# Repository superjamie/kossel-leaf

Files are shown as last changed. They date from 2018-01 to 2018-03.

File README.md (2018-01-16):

# Kossel Leaf

Kossel Leaf is a carriage system for Kossel-style delta robot 3D printers.

It uses 3D printed components, OpenBuilds-style V-wheels, OpenBuilds-style 20mm V-slot aluminium extrusions, and standard metric fasteners.

The carriage is designed to drop in place of an existing Hiwin-style MGN12H (or MGN12C) rail system, only increasing the printer’s `DELTA_RADIUS` by 0.05mm.

Kossel Leaf uses a 3D printed leaf spring to keep two wheels under tension and pressed against the extrusion firmly and evenly at all points along vertical travel, like a [SeeMeCNC Cheapskate carriage](https://www.seemecnc.com/products/injection-molded-cheapskate-carriage-set).

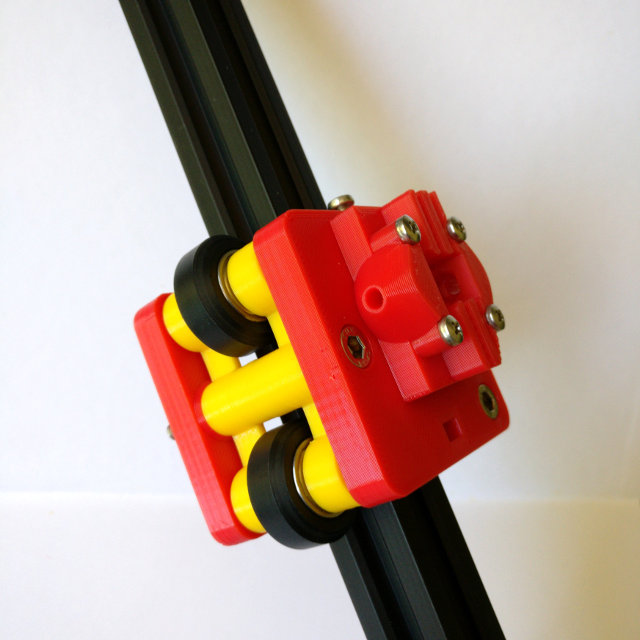
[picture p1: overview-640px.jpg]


See the included instruction manual for full BOM and assembly instructions.

## License

[CERN OHL v1.2](http://ohwr.org/cernohl)

## Author

Jamie Bainbridge - jamie.bainbridge@gmail.com

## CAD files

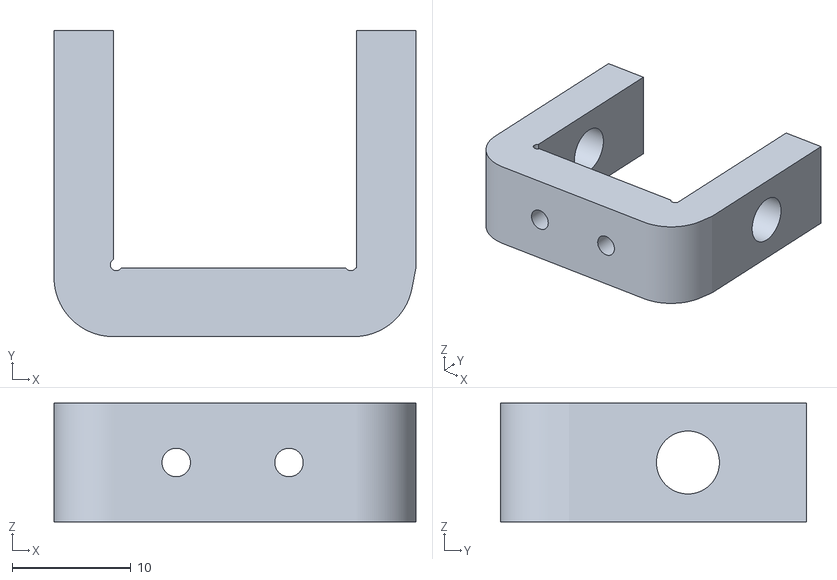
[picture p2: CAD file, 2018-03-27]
Endstop Holder for Omron SS-5GL.stl
30.5 x 25.8 x 10.0

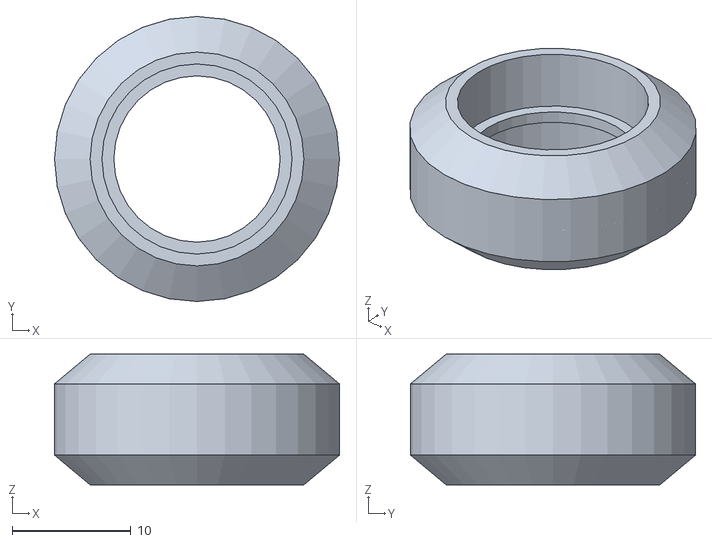
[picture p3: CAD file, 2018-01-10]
scad/parts/_wheel.stl
24.0 x 24.0 x 11.0

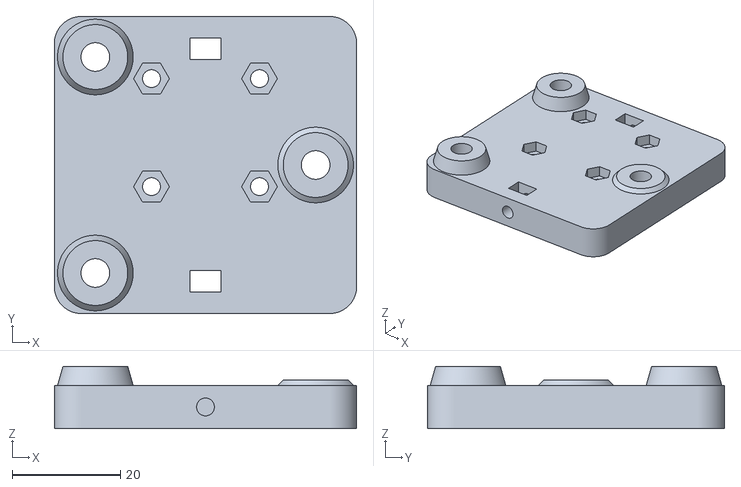
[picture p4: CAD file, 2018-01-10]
Carriage Inner.stl
56.0 x 55.0 x 11.5

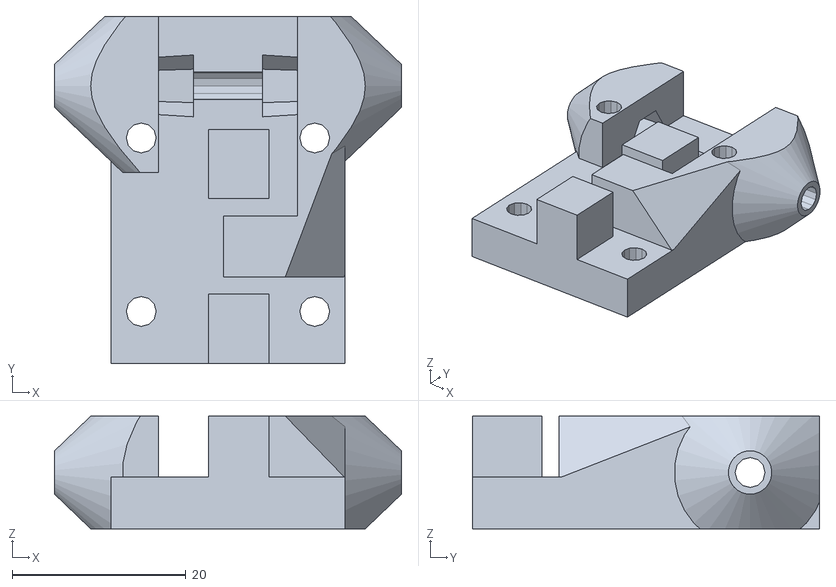
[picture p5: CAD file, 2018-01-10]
scad/parts/_belt-arm_johann.stl
40.0 x 40.0 x 13.0

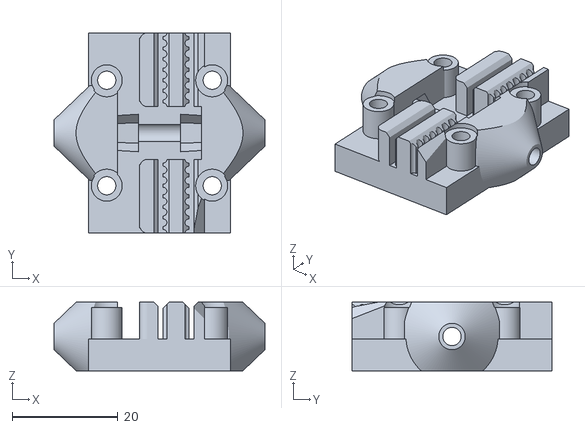
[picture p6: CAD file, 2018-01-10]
Kossel Leaf Mini 40mm Belt-Arm MGN12H.stl
40.0 x 38.0 x 13.0

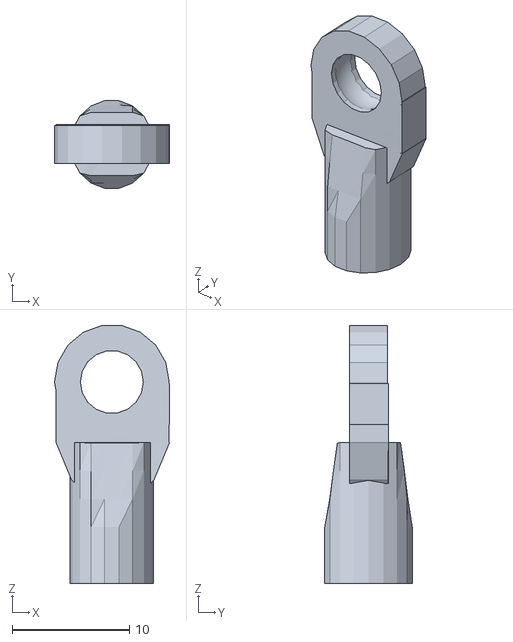
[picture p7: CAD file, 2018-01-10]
scad/parts/_tx5347.stl
9.81 x 7.47 x 22.0

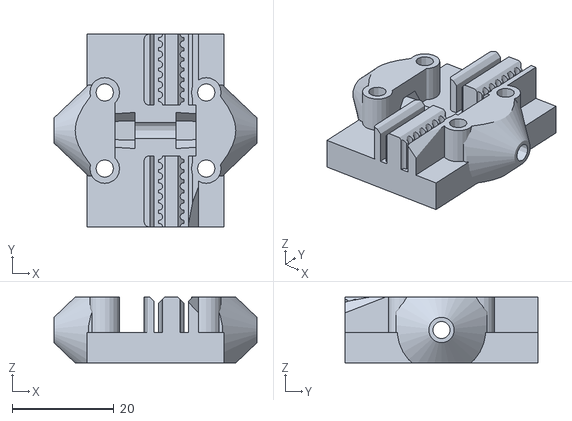
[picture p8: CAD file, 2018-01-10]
scad/parts/_belt-arm_schlotzz.stl
40.0 x 38.0 x 13.0

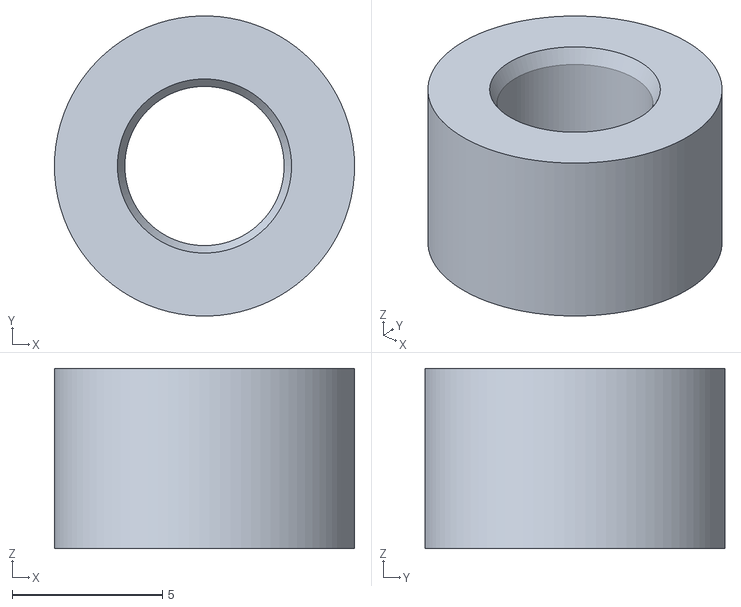
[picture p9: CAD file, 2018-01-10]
Spacer.stl
10.0 x 9.99 x 6.00

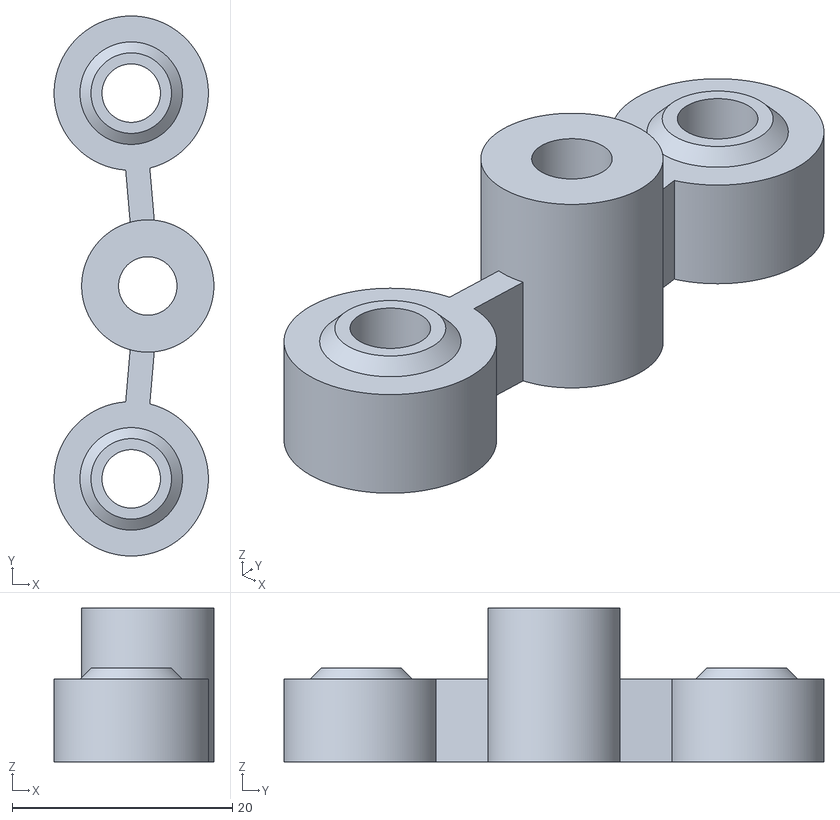
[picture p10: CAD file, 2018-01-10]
Leaf Spring Part 1 Alternate (2.2mm leaf, 1.5mm inset).stl
14.5 x 49.0 x 13.9

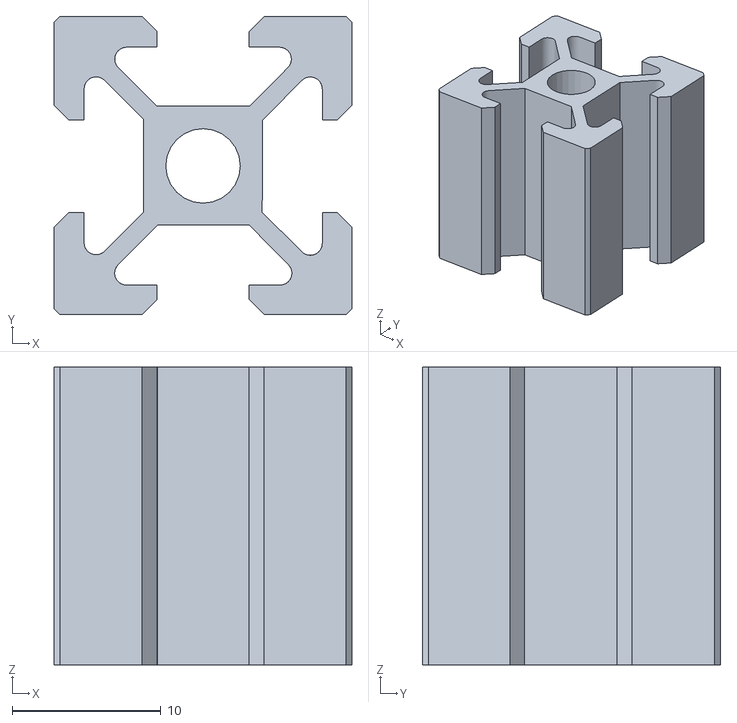
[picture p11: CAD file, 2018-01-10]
scad/parts/_vslot.stl
20.0 x 20.0 x 20.0

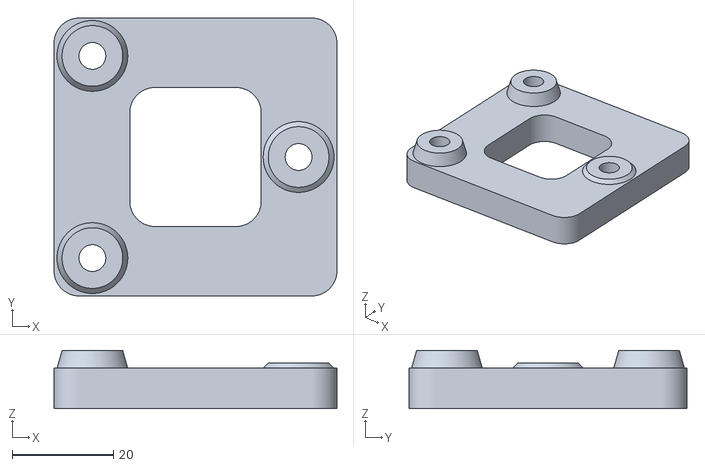
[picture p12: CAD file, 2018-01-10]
Carriage Outer.stl
56.0 x 55.0 x 11.5

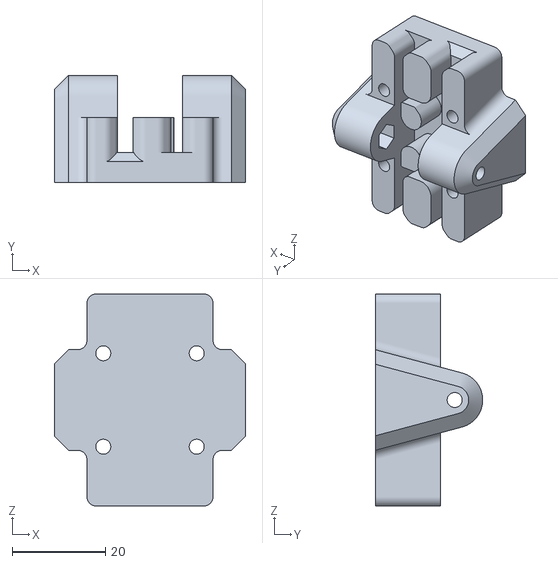
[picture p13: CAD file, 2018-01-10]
scad/parts/_belt-arm_kosselpro.stl
41.0 x 23.0 x 45.4

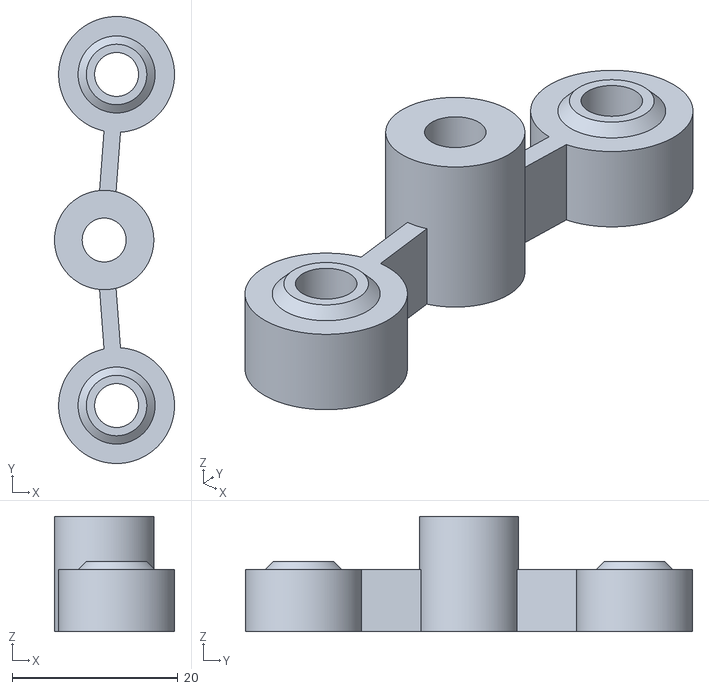
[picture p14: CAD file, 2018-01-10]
Leaf Spring Part 2 (2.0mm leaf, 1.5mm inset).stl
14.5 x 54.0 x 13.9

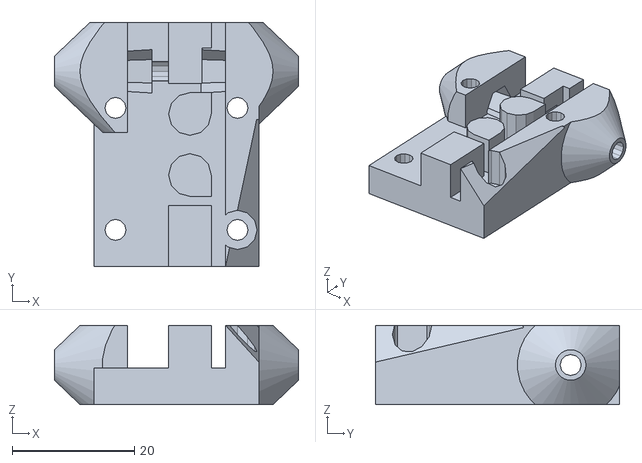
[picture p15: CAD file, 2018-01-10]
scad/parts/_belt-arm_wwchen.stl
40.0 x 40.0 x 13.0

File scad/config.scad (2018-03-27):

include <handyscad.scad>

/* global */

$fn = 36;
// need openscad nightly for this, see Issue 149
$fn = $preview ? 36 : 180;
e = 1.1; // epsilon, used for not sharing faces

/*
 * carriage
 */

// 2020 extrusion is 20mm
extrusion = 20;

// metric clearances - depending on how good your printer and tuning is
metric_thick_clearance = 0.25;
metric_round_clearance = 0.25;

// metric screw clearance holes
m2c   = 2.4;
m2_5c = 2.9;
m3c   = 3.3;
m4c   = 4.3;
m5c   = 5.3;

// metric screw socket cap diameter
m2d   = 4.0 + metric_round_clearance;
m2_5d = 4.5 + metric_round_clearance;
m3d   = 5.5 + metric_round_clearance;
m4d   = 7.0 + metric_round_clearance;
m5d   = 8.5 + metric_round_clearance; // i have 8.4

// metric screw socket cap depth
m2_5k = 2.5;
m3k   = 3.0;
m4k   = 4.0;
m5k   = 5.0; // i have 4.87 and 4.95

// metric nut diameter (flat to flat)
m3n   = 5.5 + metric_round_clearance;
m4n   = 7.0 + metric_round_clearance;
m5n   = 8.0 + metric_round_clearance; // i have 7.6

// metric nut thickness
m2_5t = 2.0 + metric_thick_clearance;
m3t   = 2.4 + metric_thick_clearance;
m4t   = 3.2 + metric_thick_clearance;
m5t   = (4.7 + 3.4) / 2; // internet says 4.7 but i have 3.4! so averaged

// metric nut width (opposite to flats)
m3w = 6.08; // i have 6.07
m4w = 7.74;
m5w = 8.87;

// metric nyloc nut thickness
m3y = 4; // i have 3.78
m4y = 5;
m5y = 5;

// metric pan head diameter
m2_5p =  5.0 + metric_round_clearance;
m3p   =  6.0 + metric_round_clearance;
m4p   =  8.0 + metric_round_clearance;
m5p   = 10.0 + metric_round_clearance;

// v-wheel
vout = 20.4; // v-wheel axle outset from extrusion centreline
vdia = 24.2; // v-wheel diameter (OB solid = 23.9, OB Delrin = 24.39)
vthi = 10.9; // v-wheel thickness, bearing-to-bearing face with shim

// v-wheel spacer
// https://www.aliexpress.com/item/20pcs-6mm-V-slot-v-wheel-aluminum-spacers-Free-shipping/32723187768.html
// OD 10mm, ID 5.1mm, Height 6.0mm

vspacerh =  6; // v-wheel metal spacer height
vspacerd = 10; // v-wheel spacer diameter

// linear rail mounts
mgn12x = 20; // MGN-12 horizontal mount distance
mgn12c = 15; // MGN-12-C vertical mount distance
mgn12h = 20; // MGN-12-H vertical mount distance
mgn12y = mgn12h; // change this if you use 20x15 carriage mounts

mgnface = 13; // distance from extrusion to MGN-12 mounting face

// plate
px = 56; // horizontal
py = 55; // vertical
pw = 10; // wheel axle inset
pay = 60; // plate axle y, cos i resized the plate but based everything off these, oops

platerad = 5; // plate outer curve radius

/* pz and ps
 * MGN12 mounting face is 13mm off extrusion.
 * so from middle of 2020 extrusion, we need 23mm to mounting face.
 * my 2x625+shim v-wheel is 10.9 thick at the bearing surfaces.
 * commercial metal v-wheel spacer/eccentric is 6mm thick.
 * 10.9 / 2 = 5.45  (from middle of extrusion to face of wheel bearing)
 * 5.45 + 6 = 11.45  (from middle of extrusion to top of spacer/eccentric)
 * 23 - 11.45 = 11.55 (from mount face to spacer, mount point thickness)
 * however, we can't print 0.05mm in Z with 0.25mm layer height
 * so i'll make it 11.5 and need to increase DELTA_RADIUS by 0.05mm
 */

ptemp1 = (mgnface + extrusion/2) - ((vthi/2) + vspacerh); // 11.55
layerheight = 0.25;
ptemp2 = round(ptemp1 / layerheight) * layerheight; // 11.50
pz = 8; // plate thickness, you can change this
ps = ptemp2 - pz; // standoff thickness

ppost = 12; // plate post diameter

axledims = [ [-vout,pay/2-pw],
             [-vout,-(pay/2-pw)],
             [+vout,0],
           ];

/*
 * leaf spring
 */

leaf_inset = 1.5;  // initial preload of leaf force
leaf_post_car_offset = 1; // height of leaf off the carriage
leaf_post_diam = 12;
leaf_post_height_wheel = ps - leaf_post_car_offset + vspacerh;
leaf_post_height_center = leaf_post_height_wheel + (vthi/2);
leaf_spring_thickness = 2;

leafdims = [ [0,0],
             [-leaf_inset,+(py/2-pw)],
             [-leaf_inset,-(py/2-pw)],
           ];

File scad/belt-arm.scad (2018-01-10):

/* Kossel Pro and Kossel Mini belt arm holder for Kossel Leaf
 *
 * Licence:
 * CC BY-SA 3.0, http://creativecommons.org/licenses/by-sa/3.0/
 *
 * Authors:
 * Johann C. Rocholl (jcrocholl) <johann@rocholl.net>
 * Dominik Scholz (schlotzz) <schlotzz@schlotzz.com>
 * Glen Harris (astfgl) <astfgl@iamnota.org>
 * K Zhang (gnahz)
 * Jamie Bainbridge (superjamie) <jamie.bainbridge@gmail.com>
 *
 * Based on:
 * https://github.com/jcrocholl/kossel/blob/master/carriage.scad
 * https://www.thingiverse.com/thing:263205
 * https://www.thingiverse.com/thing:431251
 * https://www.thingiverse.com/thing:646889
 */

// #########################
// ### IMPORTANT         ###
// ### ARM SEPARATION    ###
// ### IS DIFFERENT:     ###
// ### Kossel Mini == 40 ###
// ### Kossel Pro  == 41 ###
// #########################
separation = 41;

if (separation == 40) {
    echo(str("<b>NOTE: Building for Kossel MINI. Not for Kossel Pro!</b>"));
} else
if (separation == 41) {
    echo(str("<b>NOTE: Building for Kossel PRO. Not for Kossel Mini!</b>"));
} else {
    echo(str("<b>NOTE: Building for custom delta. Not for Kossel Mini or Kossel Pro.</b>"));
}


// i wanted the curves to look nicer
$fn = 90;

// Increase this if your slicer or printer make holes too tight.
extra_radius = 0.1;

// OD = outside diameter, corner to corner.
m3_nut_od = 6.1;
m3_nut_radius = m3_nut_od/2 + 0.2 + extra_radius;
m3_washer_radius = 3.5 + extra_radius;

// Major diameter of metric 3mm thread.
m3_major = 2.85;
m3_radius = m3_major/2 + extra_radius;
m3_wide_radius = m3_major/2 + extra_radius + 0.2;

m3_head = 5.68;
m3_head_radius = m3_head/2 + 0.2 + extra_radius;

thickness = 6;

horn_thickness = 13;
horn_x = 8;

belt_width = 5;
belt_x = 5.6;
belt_z = 7;

module carriage() {

    clearance = 0.125;

    // timing belt, up and down
    for (x = [-belt_x, belt_x])
        translate([x, 0, belt_z + belt_width / 2])
          % cube([1.7, 100, belt_width], center = true);

    difference() {
        union() {
            // main body
            translate([0, 0, thickness / 2])
                cube([27, 38, thickness], center = true);

            // ball joint mount horns
            translate([0, -16, 0])
                for (x = [-1, 1]) {
                    scale([x, 1, 1]) {
                        intersection() {
                            translate([0, 16, horn_thickness / 2])
                              cube([separation, 18, horn_thickness], center = true);
                            translate([horn_x, 16, horn_thickness / 2])
                              rotate([0, 90, 0])
                              cylinder(r1 = 14, r2 = 2.5, h = separation / 2 - horn_x);
                        }
                    }
                }

            // screws for linear slider inforcement
            for (x = [-10, 10]) {
                for (y = [-10, 10]) {
                    translate([x, y, horn_thickness / 2])
                      cylinder(r = m3_wide_radius + 1.2, h = horn_thickness, center = true);
                }
            }

            // belt clamps for GT2
            difference() {
                union() {
                    for (y = [-12, 12]) {
                        union() {
                            translate([-0.5 - clearance * 2, y, horn_thickness / 2 + 1]) cube([1, 14, horn_thickness - 2], center = true);
                            translate([-1 - clearance * 2, y, horn_thickness / 2 + 1])
                              cube([2, 14, horn_thickness - 2], center = true);
                            translate([-2 - clearance * 2, y, horn_thickness / 2 + 1])
                              cube([3, 12, horn_thickness - 2], center = true);
                            for (n = [-5.5, 5.5])
                                translate([-2 - clearance * 2, y + n, horn_thickness / 2 + 1])
                                  cylinder(r = 1.5, h = horn_thickness - 2, center = true);

                            translate([3.25 - clearance, y, horn_thickness / 2 + 1])
                              cube([5, 14, horn_thickness - 2], center = true);

                            translate([7.5, y, horn_thickness / 2 + 1])
                              cube([2, 14, horn_thickness - 2], center = true);
                        }
                    }
                }

                // tooth cutout
                for (x = [1.125 - 0.300 - clearance, 5.375 + 0.30 - clearance]) {
                    for (y = [0 : 19]) {
                        translate([x, 19 - y * 2, 6 - 0.001])
                          cylinder(r = 0.7, h = horn_thickness / 2 + 1);
                    }
                }

                // cutout for easier inserting of belt
                for (x = [0.5 - clearance, 6 - clearance])
                    translate([x, 0, horn_thickness])
                      rotate([0, 45, 0])
                      cube([2 + clearance / 2, 50, 2 + clearance / 2], center = true);

                // avoid touching diagonal push rods (carbon tube)
                translate([20, -20, 12.5])
                  rotate([35, 35, 30])
                  cube([40, 40, 20], center = true);
            }
        }

        // screws for linear slider
        for (x = [-10, 10]) {
            for (y = [-10, 10]) {
                translate([x, y, thickness])
                  cylinder(r = m3_wide_radius, h = 30, center = true);
                // recessed screws
                translate([x, y, horn_thickness + 0.5 - 0.001])
                  cylinder(r = m3_head_radius, h = 3 + 0.003, center = true);
            }
        }

        // screws for ball joints
        translate([0, 0, horn_thickness / 2])
          rotate([0, 90, 0])
          # cylinder(r = m3_wide_radius, h = 60, center = true);

            // lock nuts for ball joints
            for (x = [-1, 1]) {
                scale([x, 1, 1]) {
                    intersection() {
                        translate([horn_x, 0, horn_thickness / 2])
                          rotate([90, 0, -90])
                          cylinder(r1 = m3_nut_radius, r2 = m3_nut_radius + 0.5, h = 8, center = true, $fn = 6);
                    }
                }
            }
    }
}

carriage();

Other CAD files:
Leaf Spring Part 2 Reject (3.0mm leaf, 2.5mm inset).stl
scad/parts/_belt-arm_kumy.stl
Leaf Spring Part 1 (2.0mm leaf, 1.5mm inset).stl
Kossel Leaf Pro 41mm Belt-Arm MGN12H.stl
scad/parts/_belt-arm_astfgl.scad
scad/parts/belt-arm_schlotzz.scad
Leaf Spring Part 1 Reject (3.0mm leaf, 2.5mm inset).stl
Leaf Spring Part 2 Alternate (2.2mm leaf, 1.5mm inset).stl
scad/carriage.scad
scad/endstop.scad
scad/leafspring.scad
scad/parts.scad
scad/render.scad

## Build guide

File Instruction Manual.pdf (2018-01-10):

# Kossel Leaf

## Instruction Manual

Version 1.0 – January 2018

Copyright Jamie Bainbridge 2018

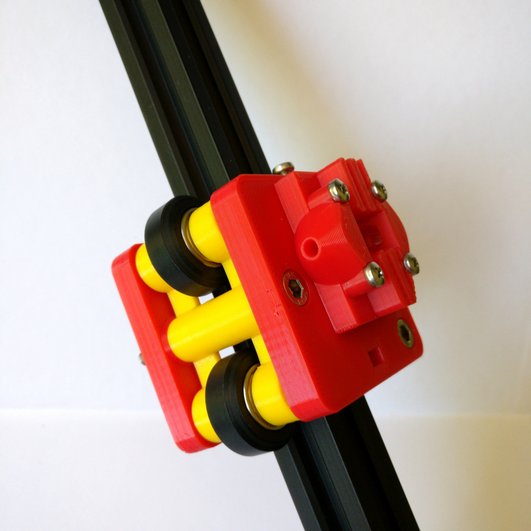
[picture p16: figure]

This documentation describes Open Hardware and is licensed under the CERN OHL v1.2 or later

You may redistribute and modify this documentation under the terms of the CERN OHL v1.2 (http://ohwr.org/cernohl). This documentation is distributed WITHOUT ANY EXPRESS OR IMPLIED WARRANTY, INCLUDING OF MERCHANTABILITY, SATISFACTORY QUALITY AND FITNESS FOR A PARTICULAR PURPOSE. Please see the CERN OHL v1.2 for applicable conditions.

Page 1 of 23

## Introduction

Kossel Leaf is a carriage system for Kossel-style delta robot 3D printers.

It uses 3D printed components, OpenBuilds-style V-wheels, OpenBuilds-style 20mm V-slot aluminium extrusions, and standard metric fasteners.

The carriage is designed to drop in place of an existing Hiwin-style MGN12H (or MGN12C) rail system, only increasing the printer’s DELTA_RADIUS by 0.05mm.

To attach belt/arm carriers, the Kossel Leaf carriage uses MGN12H mount layout of M3 screws in a 20x20mm pattern. Provision is given in the source code to easily use MGN12C mount layout of M3 screws in a 20x15mm pattern.

A major factor of Kossel carriage design with wheels is keeping firm and even wheel pressure on the extrusion as the carriage moves up and down. There are various solutions to this including eccentric spacer nuts, carriages which flex to press one wheel into the extrusion, and carriages which press wheels in with springs.

Kossel Leaf uses a 3D printed leaf spring to keep two wheels under tension and pressed against the extrusion firmly and evenly at all points along vertical travel. The leaf spring tension can be modified by printing a part with a thicker leaf, and/or moving the initial inset of the wheels inwards or outwards.

In this way, Kossel Leaf is a re-implementation of the GNU GPL-licensed Cheapskate carriage by SeeMeCNC:

https://www.seemecnc.com/products/injection-molded-cheapskate-carriage-set

Kossel Leaf carriages have an endstop adjustment screw and suit the common Omron SS-5GL style endstop switches.

This endstop adjustment screw can also be used as a mount for a flying extruder if desired.

Page 2 of 23

## Bill of Materials – Vitamins

Vitamins describe non-printed parts.

- | 9x | M5x50 Socket Head Cap Screw (45mm also acceptable)
- | 6x | M5x25 Socket Head Cap Screw
- | 15x | M5 Nyloc Nut
- | 3x | M3 Nyloc Nut
- | 3x | M3x12 to M3x20 Screw (SHCS, Pan head, Button head all suitable)
- | 12x | OpenBuilds-style solid V-wheel - 5mm axle, OD 23.9 to 25mm
http://openbuildspartstore.com/solid-v-wheel-kit/
- | 3x | OpenBulds-style V-slot 20mm extrusion, length determined by your printer and needs
http://openbuildspartstore.com/v-slot-20x20-linear-rail/
- | 3x | Omron SS-5GL microswitch, or other equivalent with M2.5 mounting screws spaced 9.5mm apart
- | 6x | M2.5x12 to M2.5x20 Screw (SHCS, Pan head, Button head all suitable)
- | 6x | M2.5 Nut

## Bill of Materials – Printed or Vitamin

You can either print or purchase these parts, choose one or the other.

- | 12x | V-wheel spacer: Height 6.0mm, ID 5.1mm, OD 10mm
https://www.aliexpress.com/item/10-PCS-for-v-slot-Openbuilds-Isolation-Column-Separate-Pillar-Quarantine-Bore-5-5-1mm-Thickness/32820502527.html
| OR
- | 12x | Spacer.stl

Page 3 of 23

## Bill of Materials – Belt-Arm Carriages

If you wish to use Traxxas 5347 rod-ends on Johann Kossel-style belt-arm holders, included are STLs for Kossel Mini (40mm arm spacing) and Kossel Pro (41mm arm spacing). You could use these, or a different design of Johann-style carriage, or metal belt-arm holders from 3D printer vendors.

- | 3x | Belt Arm holders, depending on your printer
- | 4x | M3 Nut
- | 4x | M3x20 Screw (SHCS, Pan head, Button head all suitable)

If you are using magnetic arms or ball joint arms, you’ll need a different belt-arm holder to suit your arms, and probably different screw lengths.

## Bill of Materials – Printed Parts

3x | Carriage Inner.stl
3x | Carriage Outer.stl
3x | Leaf Spring Part 1.stl
3x | Leaf Spring Part 2.stl
3x | Endstop Holder for Omron SS-5GL.stl

### Print Material

The carriages can be printed in whatever solid (non-flexible) material you prefer.
Common 3D printer component choices like PLA, ABS, PETG, PC would all be suitable. The stiffer the carriage parts are, the better.

The leaf springs are intended to be printed in PETG. Do not print the leaf springs in PLA!

PETG is chosen as it has a high flexural strength, low flexural modulus, and high elongation at yield.
This means that PETG is “bendy” and can be deformed slightly and for long periods without cracking.

PLA leaf springs would be unacceptable. PLA has a high flexural modulus and low elongation at yield.
This means PLA is stronger, but will crack if bent too much or held in tension over time.

From reading material datasheets, polycarbonate (PC) and Taulman T-glase (PETT) appear to be acceptable substitutes for PETG.

ABS, Nylon, or Amphora 1800 (Taulman n-Vent) may be suitable. Tried these materials have not been tried at the time of writing.

Page 4 of 23

### Print Settings

Parts have been tested in both Slic3r and Cura with:

- 0.4mm nozzle
- 0.48mm extrusion width
- 0.25mm layer height
- 4 external perimeters
- 8 top and bottom layers
- 50% infill

If using a finer nozzle where 0.25mm layer height is not possible, ensure the selected layer height can print 0.5mm height accurately.

This means the only other realistic options are 0.125mm or 0.1mm layer heights.

Page 5 of 23

## Assembly

Instructions are given for one carriage. The other two carriages are identical, just repeat the steps.

Gather parts pictured:

2x | M5x25 SHCS
2x | M5 Nyloc Nut
2x | Wheel
| Leaf Spring Part 1
| Leaf Spring Part 2

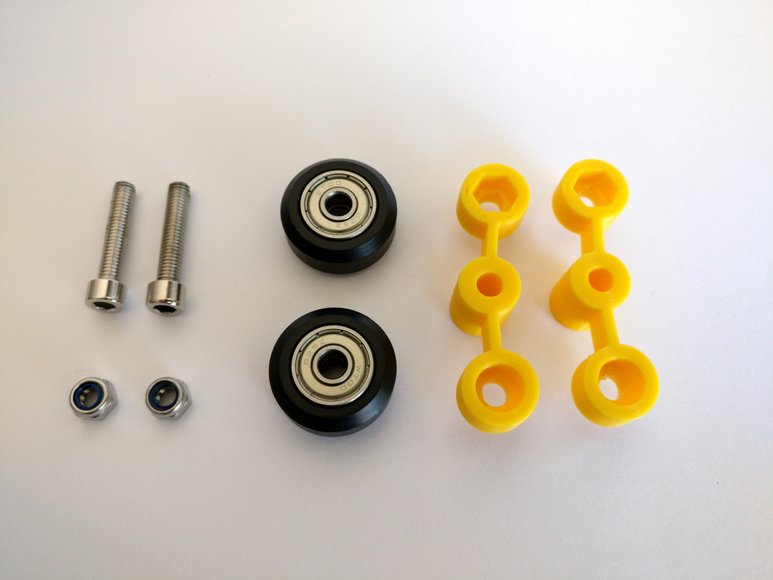
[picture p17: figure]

Page 6 of 23

Insert one screw into the round hole in the Leaf Spring.

Put one wheel on the screw.

Page 7 of 23

Place the other Leaf Spring on top.

The screw end should now be in a hexagonal nut trap.

Page 8 of 23

Insert a nyloc nut and fasten.

Ensure the wheel can still spin.

The end of the screw should be about even with the nut body.

Page 9 of 23

Flip the assembly over.

Insert the screw and wheel into the other hole.

Page 10 of 23

Add the remaining Nyloc nut.

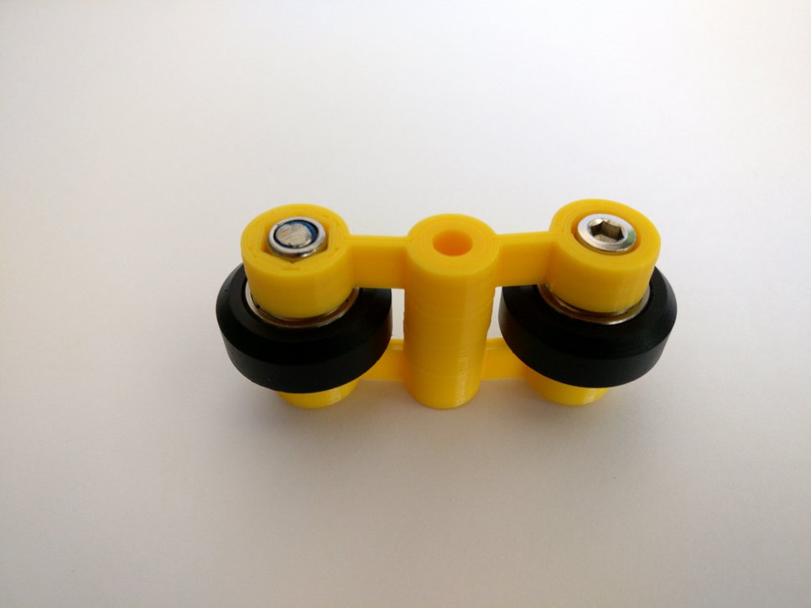
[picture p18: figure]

Ensure the two halves of the leaf touch in the middle with no play, the screws are on their nuts with no play, and the wheels can still spin freely.

Page 11 of 23

Gather parts pictured:

3x | M5x50 SHCS
3x | M5 Nyloc Nut

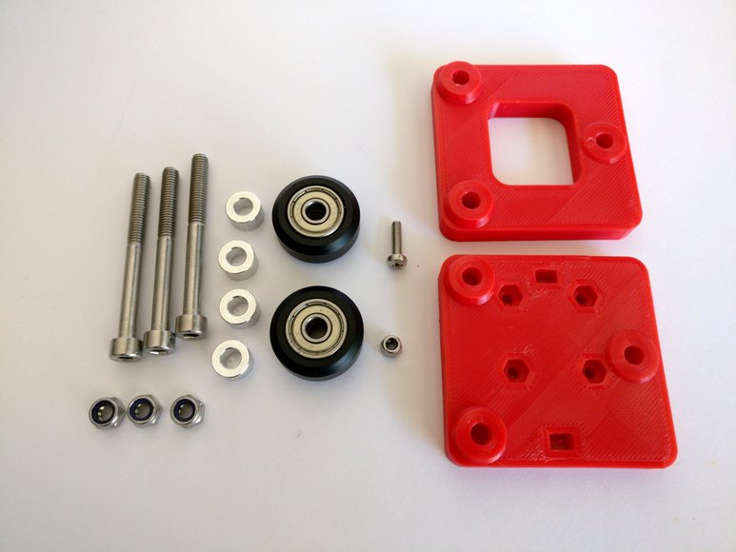
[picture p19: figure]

4x | 6mm spacer (aluminium spacer pictured, you may have printed these)
2x | Wheel
| M3x12 Screw
| M3 Nyloc Nut
| Carriage Outer
| Carriage Inner

Page 12 of 23

Insert M5x50 screws into Carriage Inner.

Page 13 of 23

Place 2 spacers onto the tallest carriage pillars.

These are the pillars with the fixed (non-leaf) wheels.

Page 14 of 23

Place two wheels on top of the spacers.

Page 15 of 23

Place the other two spacers on top of the wheels.

Page 16 of 23

Fit the Carriage Outer to the screws.

Page 17 of 23

Insert and fasten Nyloc nuts for the two fixed wheels.

Ensure the screw has no play back and forth, and that the wheels can spin freely.

Don’t put a nut on the other screw just yet!

Page 18 of 23

Remove the remaining M5x50 screw, and get the leaf spring assembly created earlier.

Page 19 of 23

Install the leaf spring assembly in between the carriage plates.

It doesn’t matter which way you install the spring, it can rotate to the “correct” and “incorrect” orientation.

Insert the M5x50 screw to hold the leaf spring in place. Fasten with the remaining M5 Nyloc nut (not pictured).

Page 20 of 23

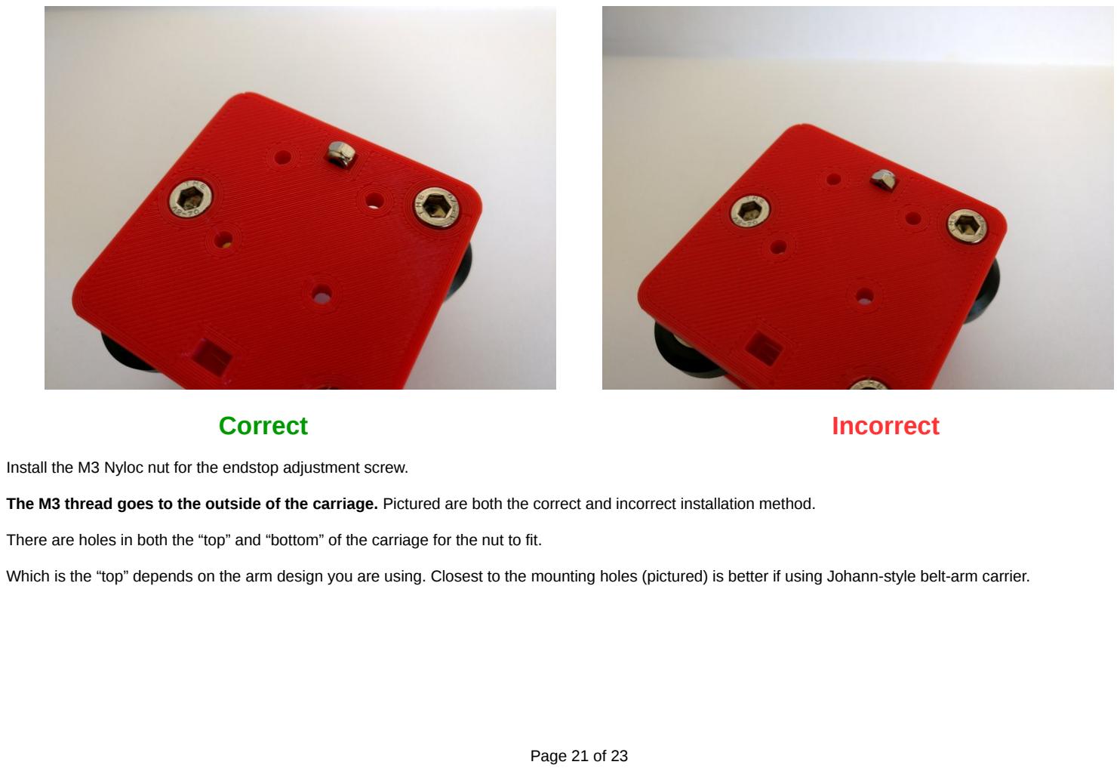
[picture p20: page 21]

Correct | Incorrect

Install the M3 Nyloc nut for the endstop adjustment screw.

The M3 thread goes to the outside of the carriage. Pictured are both the correct and incorrect installation method.

There are holes in both the “top” and “bottom” of the carriage for the nut to fit.

Which is the “top” depends on the arm design you are using. Closest to the mounting holes (pictured) is better if using Johann-style belt-arm carrier.

Page 21 of 23

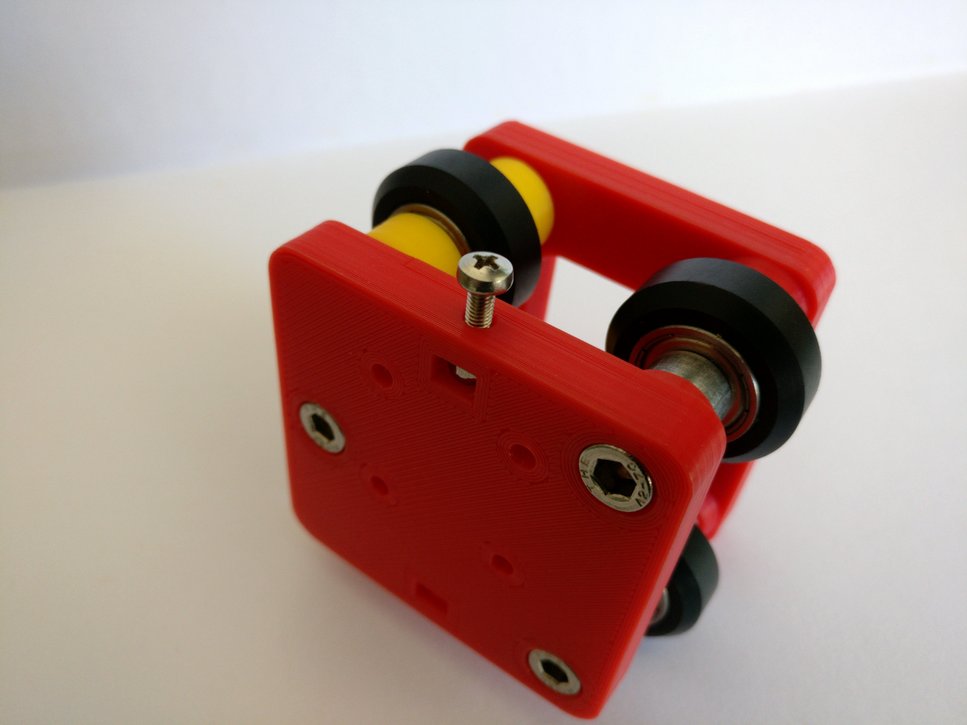
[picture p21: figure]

Install the M3 endstop adjustment screw.

Ensure the M3 Nyloc nut cannot rotate.

If the nut can rotate, remove it and wrap it with something like kapton tape or blue tape to increase the nut diameter.

Ensure the nut is really strongly fixed in there and cannot move at all.

Page 22 of 23

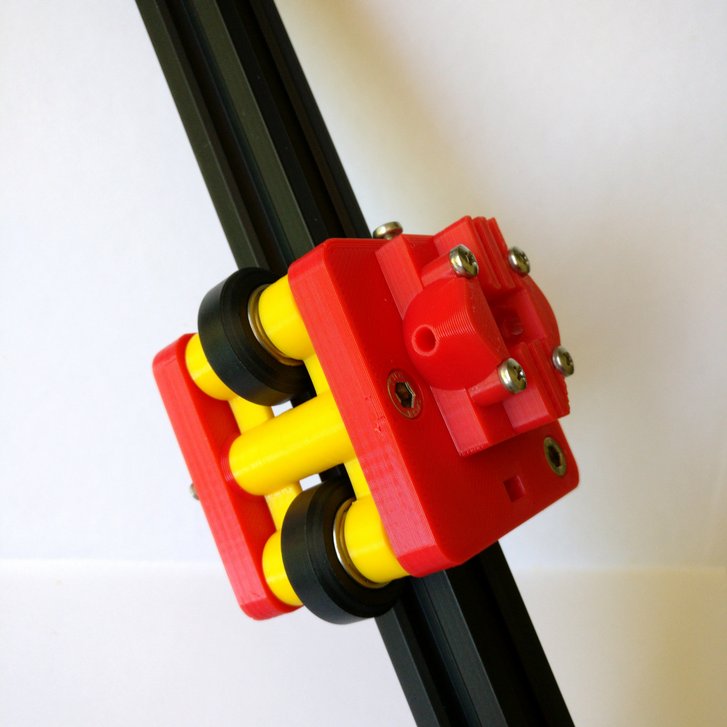
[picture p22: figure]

Install the entire assembly onto V-slot extrusion.

Ensure the wheels press firmly on the extrusion.

If the wheels are sloppy and the carriage can rattle around, remove the carriage, rotate the leaf spring 180 degrees on its axle, and reinstall onto the extrusion.

Assembly complete.

Page 23 of 23

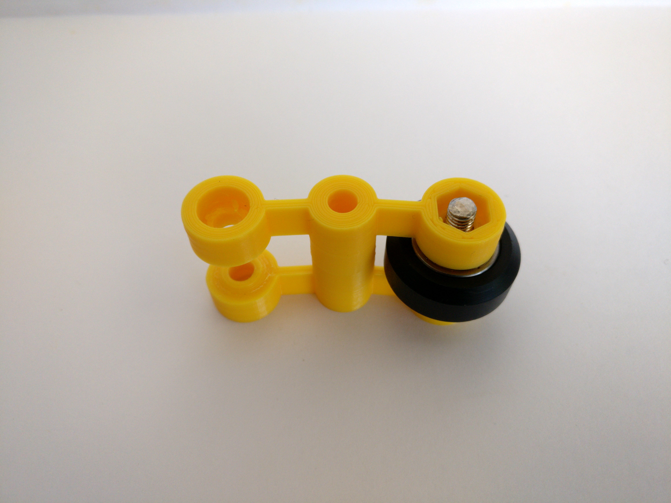
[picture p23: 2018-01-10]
manual-src/leaf-02.jpg

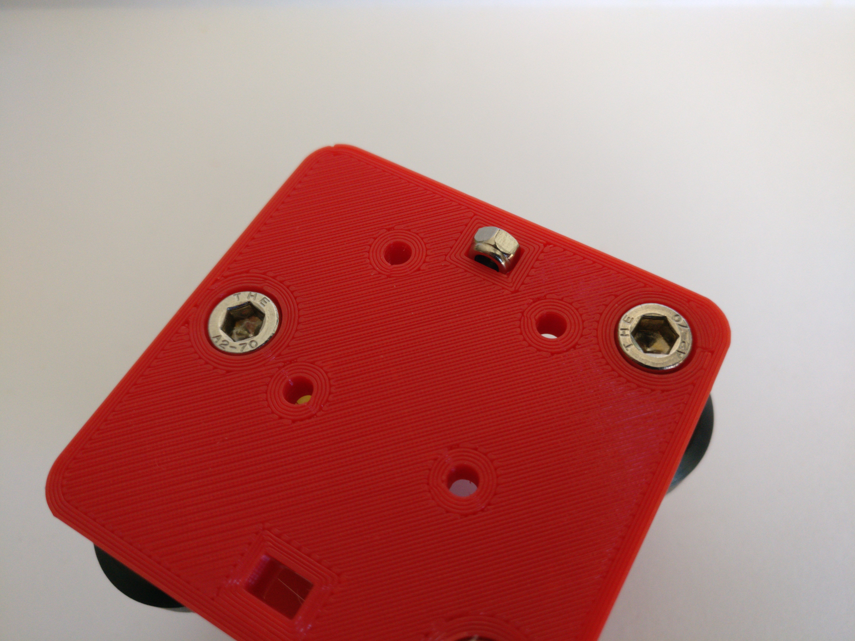
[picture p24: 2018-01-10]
manual-src/orig/car-09-yes.jpg

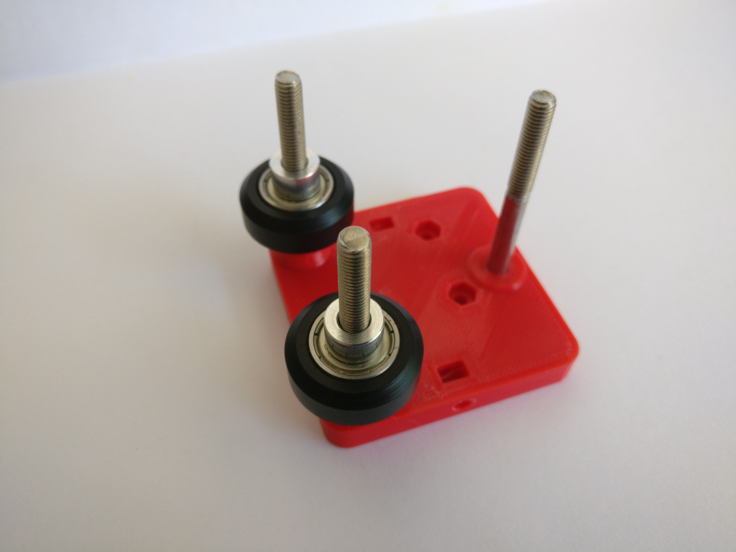
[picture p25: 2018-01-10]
manual-src/orig/car-04.jpg

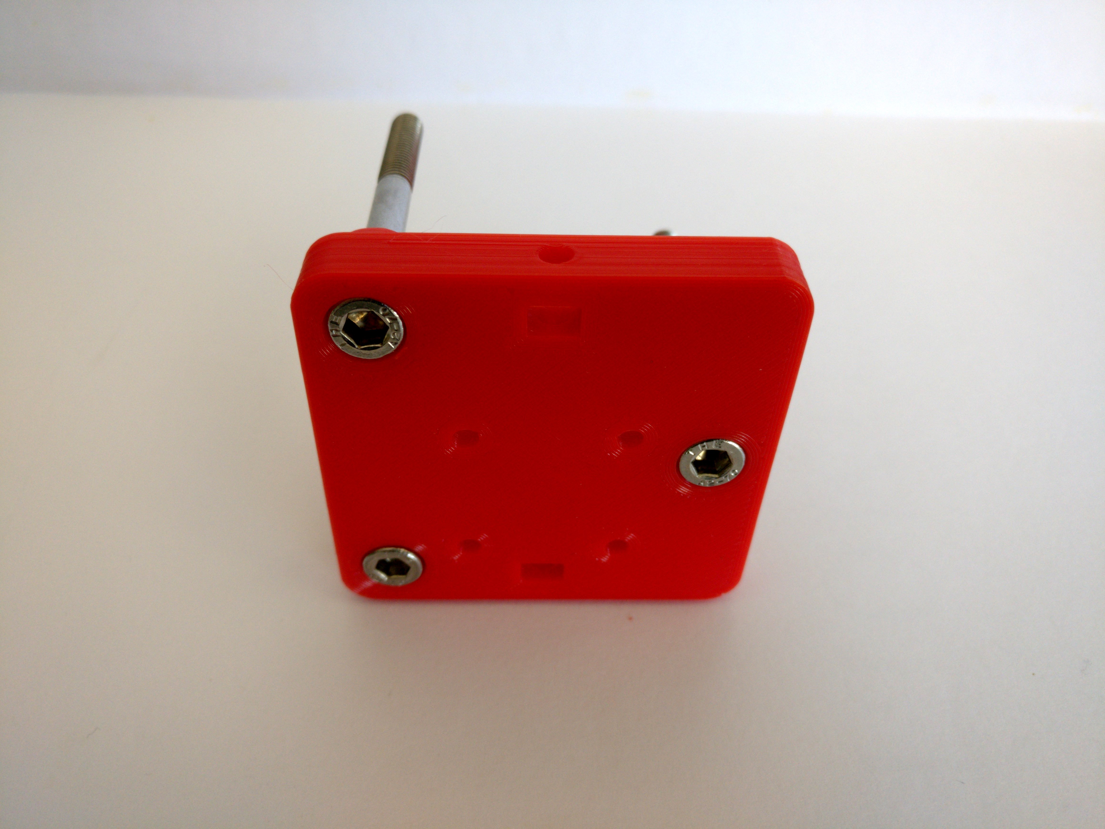
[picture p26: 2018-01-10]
manual-src/car-01.jpg

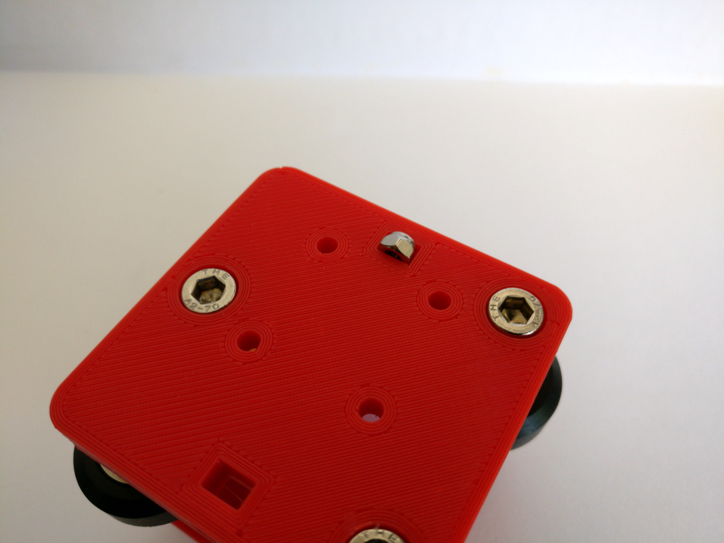
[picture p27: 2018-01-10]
manual-src/car-09-no.jpg

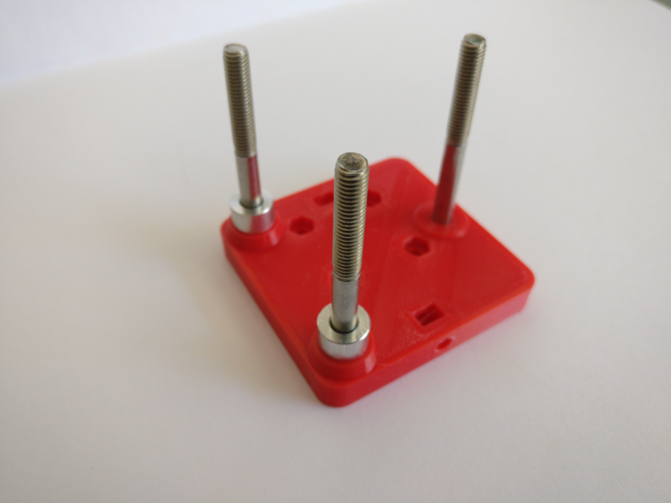
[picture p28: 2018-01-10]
manual-src/orig/car-02.jpg
